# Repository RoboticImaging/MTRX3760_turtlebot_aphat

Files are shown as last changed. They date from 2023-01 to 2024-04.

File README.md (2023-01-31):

# MTRX3760 AP Hat Code + Documentation
Code for MTRX3760 AP Hat

## Code
The code found in this repo (in the `code` folder) is on each Turtlebot in a hidden `.mtrx` folder found at `/home/ubuntu/`.

This is used in conjunction with the following lines in the Turtlebot crontab to automatically set hostname, change network state using hardware switch and indicate status live using an LED. You can edit the crontab if needed by running `crontab -e`. You can check the following lines are listed by running `crontab -l`.

```bash

@reboot /home/ubuntu/.mtrx/set_hostname.sh &
@reboot python3 /home/ubuntu/.mtrx/change_wifi.py &
@reboot python3 /home/ubuntu/.mtrx/status_LEDs.py &

```

Students will interface with 2 scripts that can reset and add WiFi networks. These are provided in the `home_files` folder and are to be placed at `/home/ubuntu/`. They are also shipped in the content for the `.mtrx` folder as a backup should they ever be deleted.

## MOTD
We also have additional code which spits out the MAC Address for the Turtlebot and provides a brief welcome message to students. This is included in `/etc/update-motd.d/99-mtrx-mac`. If altering or reconfiguring, you will need to ensure you change permissions such that this file is executable (i.e. `chmod +x` it). This is also provided in the motd folder of this repo.

```bash
#!/bin/sh

IFACE=wlan0
read mac_address </sys/class/net/$IFACE/address

echo "$(tput -T xterm setaf 1)Welcome to MTRX @ The University of Sydney$(tput -T xterm sgr0)"
printf "\nThis is a Turtlebot3 Burger. Please report any issues to your tutor at first boot.\n"

echo "Turtlebot3 has MAC Address: $(echo $mac_address)."
```

## PCB Design
All PCB design files, BOM and circuit schematics are provided in the `pcb_design` folder. These were designed and provided by Tony Cimino of ACFR's tech staff.

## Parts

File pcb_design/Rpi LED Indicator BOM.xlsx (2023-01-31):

Name | Description | Designator | Quantity | Manufacturer 1 | Manufacturer Part Number 1 | Supplier 1 | Supplier Part Number 1
Red | LED RED 0603 SMD | D1 | 1 | WE | 5973005507F | DigiKey | 350-4374-1-ND
Green | LED GREEN DIFFUSED CHIP SMD | D2 | 1 | WE | HSMG-C197 | DigiKey | 516-2830-1-ND
Blue | LED BLUE 0603 SMD | D3 | 1 | WE | 5973604507F | DigiKey | 350-4381-1-ND
Rpi Connector | female 6ckt | J1 | 1 | Sullins | PPPC032LFBN-RC | DigiKey | S7106-ND
Res 0603 | 200R, 0603 | R1, R2, R3 | 3 | Stackpole | RMCF0603FT200R | DigiKey | RMCF0603FT200RCT-ND
Res 0603 | 10k, 0603 | R4 | 1 | Stackpole | RMCF0603FT10K0 | DigiKey | RMCF0603FT10K0CT-ND
Switch SDPT | SWITCH SLIDE SPDT | S1 | 1 | Nidec Copal | CL-SB-12A-11T | DigiKey | 563-1316-1-ND
M2.5 socket head cap screw, 6mm |  |  | 1
M2.5 hex standoff, 12mm |  |  | 1

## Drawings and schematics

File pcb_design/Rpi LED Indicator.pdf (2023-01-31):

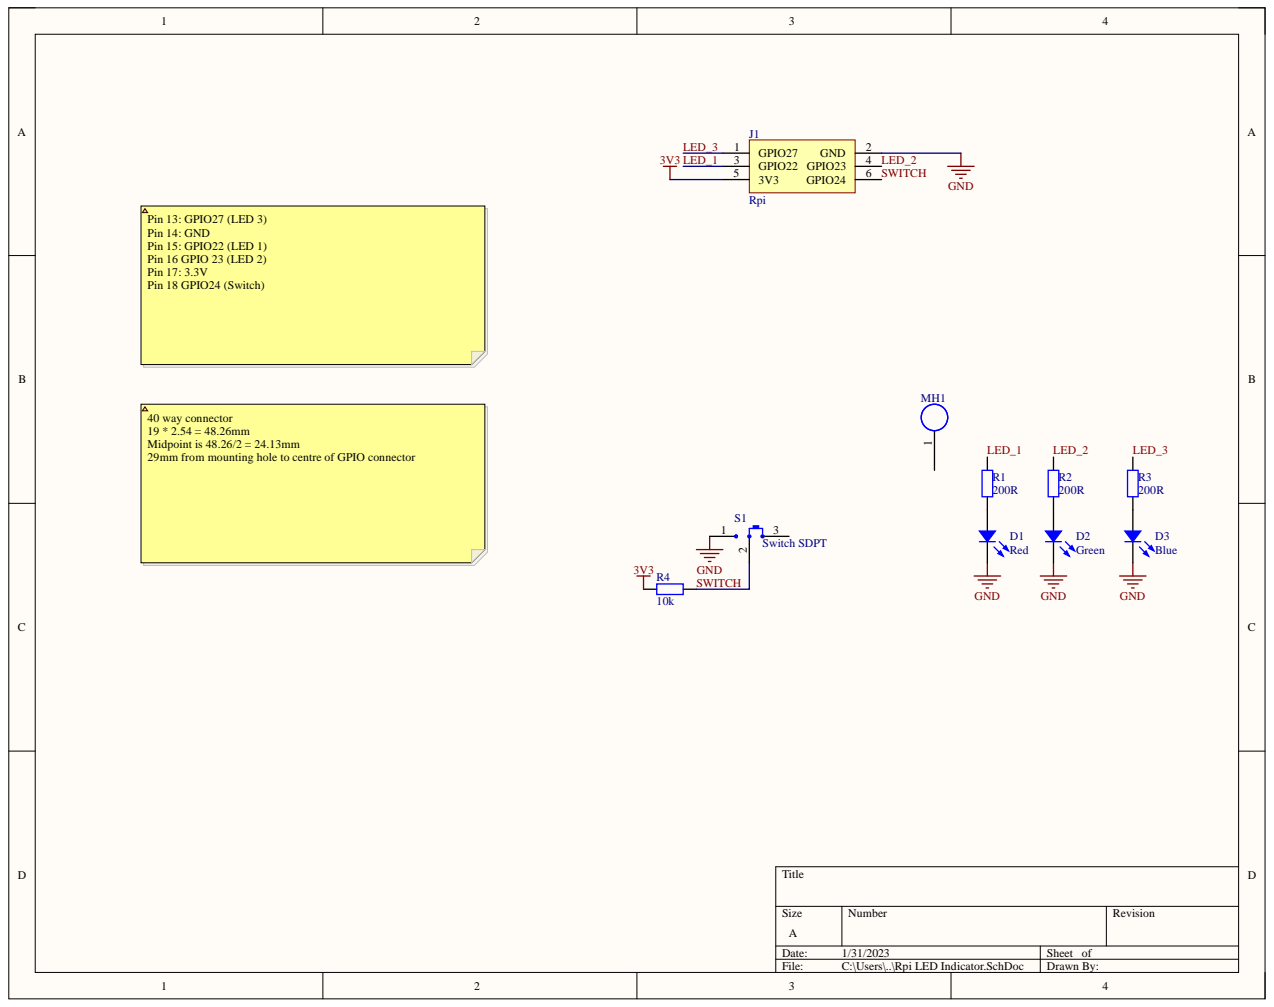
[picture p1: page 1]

40 way connector
Midpoint is 48.26/2 = 24.13mm
29mm from mounting hole to centre of GPIO connector

Size A | Number | Revision

Date: 1/31/2023 | Sheet of
File: C:\Users\..\Rpi LED Indicator.SchDoc | Drawn By:

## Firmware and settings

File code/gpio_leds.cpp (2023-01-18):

/*
* GPIO LEDs - Turtlebot Ambulance
*
* A very simple program demonstrating how to use the GPIO pins from C++
*
* Compile using: g++ gpio_leds.cpp -lgpiodcxx -o led_test
* Run using: sudo ./led_test
*
* This code depends on libgpiod-dev (there are alternatives equally as capable).
*
* Author: Jack Naylor, Australian Centre for Field Robotics 2023
* Email: jack.naylor@sydney.edu.au
*/



#include <chrono>
#include <iostream>
#include <thread>

#include <gpiod.h>
#include <gpiod.hpp>

using namespace std::literals::chrono_literals;

const int bLedPin = 27;
const int rLedPin = 22;

int main (void)
{
  std::cout << "ACTIVATE: TURTLEBOT AMBULANCE (PROTOTYPE V0.5)\n";
  std::cout << "Be advised the medical capability of this ambulance is severely limited.\n";

  std::this_thread::sleep_for(2000ms);

  gpiod::chip chip("gpiochip0");
  auto line1 = chip.get_line(bLedPin);
  line1.request({"blue_led",
                 gpiod::line_request::DIRECTION_OUTPUT, 
                 0}, 0);
  auto line2 = chip.get_line(rLedPin);
  line2.request({"red_led",
                 gpiod::line_request::DIRECTION_OUTPUT, 
                 0}, 0);
  while (true) {
    line1.set_value(1);
    line2.set_value(0);
    std::cout << "WEEE" << std::endl;
    std::this_thread::sleep_for(200ms);
    line2.set_value(1);
    line1.set_value(0);
    std::cout << "AWWWW" << std::endl;
    std::this_thread::sleep_for(200ms);
  }

  return 0 ;
}

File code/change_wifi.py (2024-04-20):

"""
This script runs from a CronJob at reboot in an infinite loop, detecting the state of the AP Hat switch.
If the Turtlebot is already in a state, no actions are taken, but should the state change the netplan
used by the turtlebot is updated to a different mode, and re-applied.

Updates to the netplan may take a moment or two to come into effect. Note the status LED is separate
to this script and operates on the actual state of the network at each point in time.

Created: 25/11/2022
Authors: Jack Naylor & Ryan Griffiths
Updated for 2024: Jack Naylor
"""

import RPi.GPIO as GPIO
import os
import time

GPIO.setwarnings(False)
GPIO.setmode(GPIO.BOARD)
GPIO.setup(18, GPIO.IN)


def main():
	# Set as an access point initially, fix undefined behaviour if no AP Hat.
	os.system('sudo cp /home/ubuntu/.mtrx/ap.yaml /etc/netplan/turtlebot_netplan.yaml')
	print("Changing to Access Point")
	os.system('sudo netplan apply')
	while True:
		# GPIO.wait_for_edge(button, GPIO.FALLING)
		with open('/etc/netplan/turtlebot_netplan.yaml') as f:
			current_mode = f.readline().strip('\n')
		print(current_mode)

		if GPIO.input(18) == 0:
			if current_mode != "#AccessPoint":
				os.system('sudo cp /home/ubuntu/.mtrx/ap.yaml /etc/netplan/turtlebot_netplan.yaml')
				print("Changing to Access Point")
				os.system('sudo netplan apply')
		else:
			if current_mode != "#Wifi":
				os.system('sudo cp /home/ubuntu/.mtrx/wifi.yaml /etc/netplan/turtlebot_netplan.yaml')
				print("Changing to Wifi")
				os.system('sudo netplan apply')
		time.sleep(5)

	GPIO.cleanup()


if __name__ == "__main__":
	main()

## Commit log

2023-01-31 PCB design docs and files
    [Rpi LED Indicator BOM.xlsx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]
2023-02-03 Fix undefined behaviour with no AP Hats.
    [change_wifi.py]
2024-04-20 bug fixing and updates
    [add_wifi.py, change_wifi.py, status_LEDs.py]
